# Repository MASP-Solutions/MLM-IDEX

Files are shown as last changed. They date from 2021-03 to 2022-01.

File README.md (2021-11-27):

# MLM-IDEX<br/>
MLM IDEX is a mod for Ben Levi's BLV MGN CUBE Project
<br/>
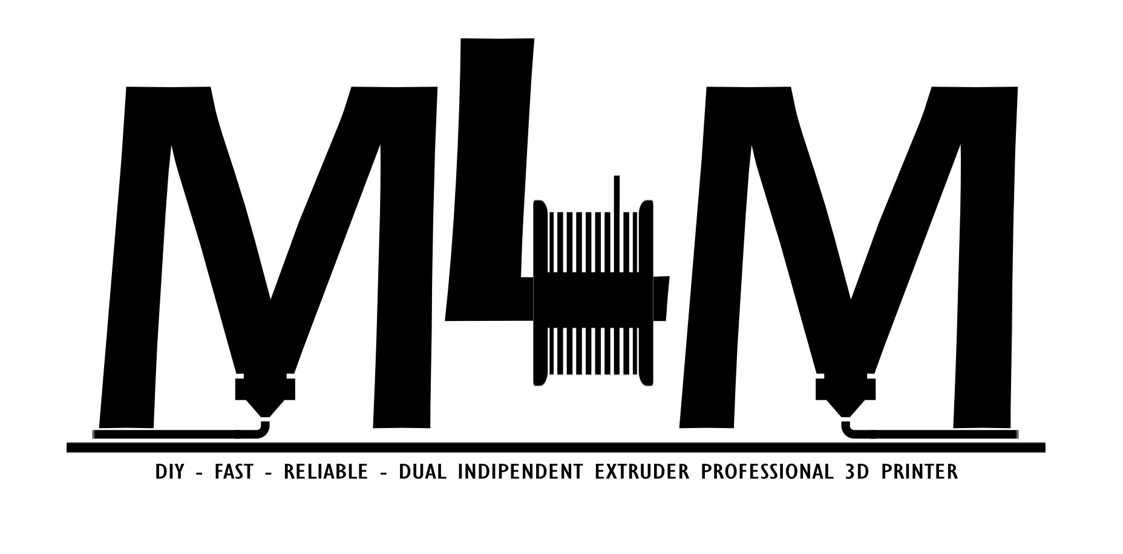
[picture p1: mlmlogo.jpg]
<br/>
<br/>
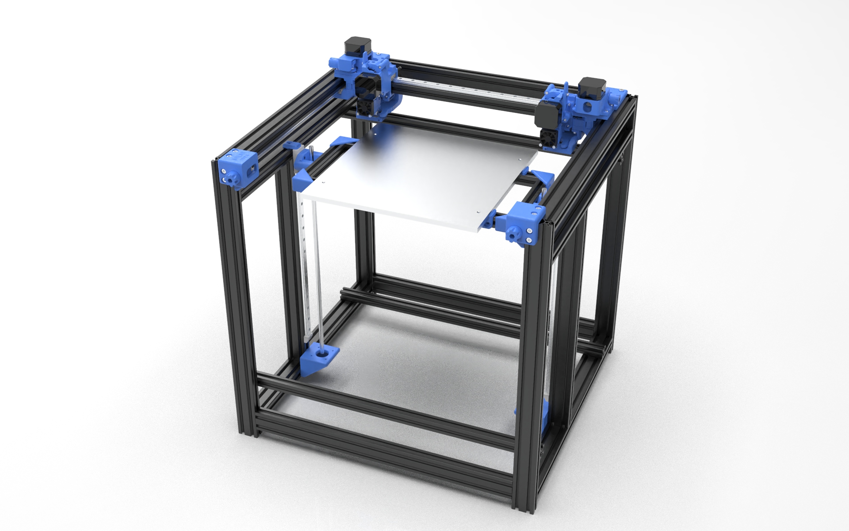
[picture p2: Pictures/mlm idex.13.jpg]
<br/>

## English<br/>
BLV MLM IDEX is a italian project started in August 2020 in collaboration with Maicol Spazzini (MASP-Solutions), Loris Granatella and Mario Salerno.<br/> 
We redesigned Ben Levi's BLV MGN Cube and created an IDEX version.<br/> 
This printer allows you to create copy, mirror and IDEX configuration prints (using two different colours or materials).<br/>
The MLM IDEX is equipped with MASP Hotend MK8-R All Metal with adjustable titanium throat, Duet 2 Wi-Fi, Duex5.<br/>
The X and U axes are driven by powerful LDO Motors 0.9° 1.4A pancakes that allow 800/step rotations.<br/>
The same ones are also used for E0 and E1, combined with a specially designed dual drive system.<br/>
The Y-axis is driven by two Wantai 0.9° 2.4A motors working in pairs: the advantage is the possibility to move the x/u bridge at high speeds and without uncertainties, also thanks to the use of a robust 9mm reinforced GT2 belt (Gates Powergrip).<br/>
Regarding the X- and U-axes, 6mm GT2 (Gates Powergrip) belts were used to reduce space requirements and to have less moving mass than the Y-axis.<br/>
A cleaning system tied to the X/U bridge ensures that the inactive tool nozzle can purge outside the plate (tool parking area) and cleans the nozzle before it enters the printing area.<br/>
The calibration of the Z offset, for "Tool 0" (i.e. X), is semi-automatic thanks to the use of a contact probe (BLTouch) and a procedure written by us ad hoc to facilitate the operation. As for the "Tool 1" (i.e. U) the calibration of the Z offset is manual, effectively facilitated by the constructive conformation of the MASP MK8-R hotend.<br/>
It is possible to choose between two or three trapezoid screws, driven by powerful Wantai 1.8° 2.5A motors.<br/>
The plate heater is a 600W - 220V "membrane" type, the top is made of 6mm aluminium.<br/>
The project is open source, all the necessary parts are freely available for purchase and printing.<br/>
The project provides all the files for the configuration that we have developed after months of testing.<br/>
## [Watch the project in 3D](https://a360.co/3cTrbso) 

## Italiano<br/>
MLM IDEX è un progetto nato ad Agosto 2020 in collaborazione con Maicol Spazzini (MASP-Solutions),  Loris Granatella e Mario Salerno, nel quale abbiamo riprogettato la BLV MGN Cube di Ben Levi creandone una versione IDEX.<br/> 
Questa stampante permette di creare stampe in copia, in mirroring e stampe in configurazione IDEX (due colori o materiali differenti).<br/>
MLM IDEX è equipaggiata con MASP Hotend MK8-R All Metal con gola in titanio regolabile, Duet 2 Wi-Fi, Duex5.<br/>
Gli assi X ed U sono azionati da potenti pancake LDO Motors 0,9° 1.4A che permettono di avere 800/step giro, gli stessi sono utilizzati anche per E0 ed E1, abbinati ad un sistema dual drive realizzato ad hoc.<br/>
L'asse Y è azionato da 2 motori Wantai 0,9° 2,4A che lavorano in coppia, a vantaggio di ciò, la possibilità di muovere il ponte X/U senza incertezze e ad alte velocità, garantito anche dall'impiego di una robusta cinghia da 9mm rinforzata di tipo GT2 (Gates Powergrip).
Per quanto concerne gli assi X ed U, sono state impiegate cinghie da 6mm di tipo GT2 (Gates Powergrip) per ridurre gli ingombri e per la minor massa in movimento rispetto all'asse Y.<br/>
Un sistema di pulizia vincolato al ponte X/U fa in modo che l'ugello del tool non attivo possa spurgare al di fuori del piatto (tool parking area) e pulisce l'ugello prima del suo ingresso nell'area di stampa.
La calibrazione dell'offset Z, per il "Tool 0" (ovvero X), è semiautomatica grazie all'impiego di una probe a contatto (BLTouch) e ad una procedura scritta da noi ad hoc per facilitare l'operazione, per quanto riguarda il "Tool 1" (ovvero U) la calibrazione dell'offset Z è manuale, agevolata efficacemente dalla conformazione costruttiva dell’hotend MASP MK8-R.<br/>
E' possibile scegliere se movimentare l'asse Z servendosi di due o tre viti trapezie, azionate da potenti Wantai 1.8° da 2.5A.<br/>
Il riscaldamento del piatto è di tipo a "membrana" da 600W - 220V, il piano in alluminio fresato da 6mm.<br/>
Il progetto è open source, tutte le parti necessarie alla realizzazione del progetto sono liberamente acquistabili e stampabili.<br/>
Il progetto mette a disposizione tutti i file per la configurazione che abbiamo messo a punto dopo mesi di collaudo.<br/>
## [Esplora il progetto in 3d](https://a360.co/3cTrbso)

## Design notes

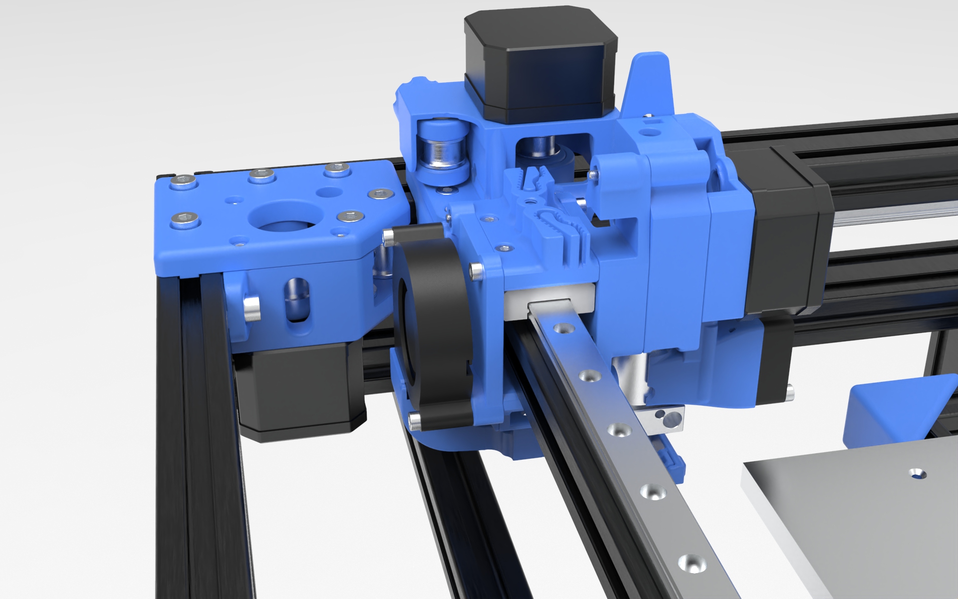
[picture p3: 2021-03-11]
Pictures/mlm idex.17.jpg

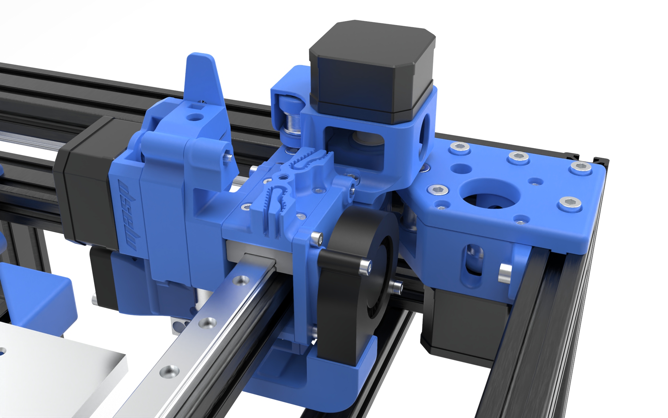
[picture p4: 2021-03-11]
Pictures/mlm idex.16.jpg

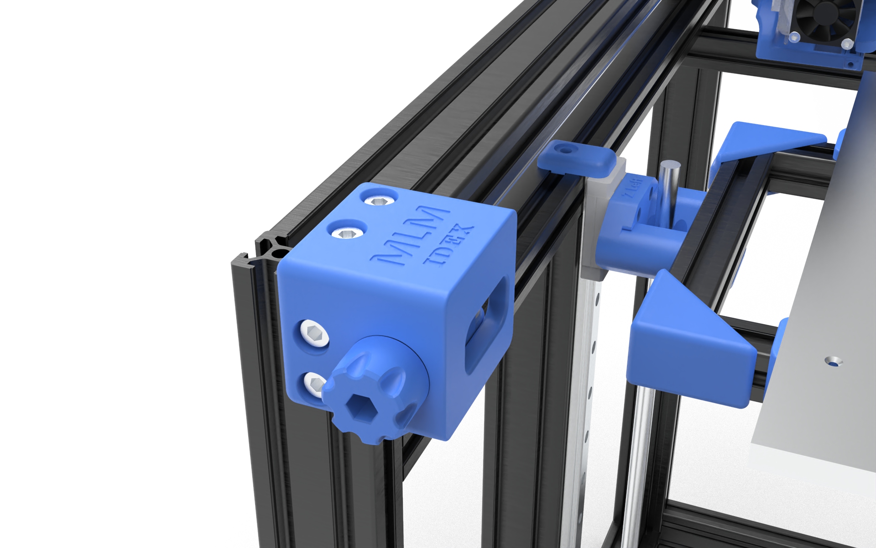
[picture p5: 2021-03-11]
Pictures/mlm idex.14.jpg

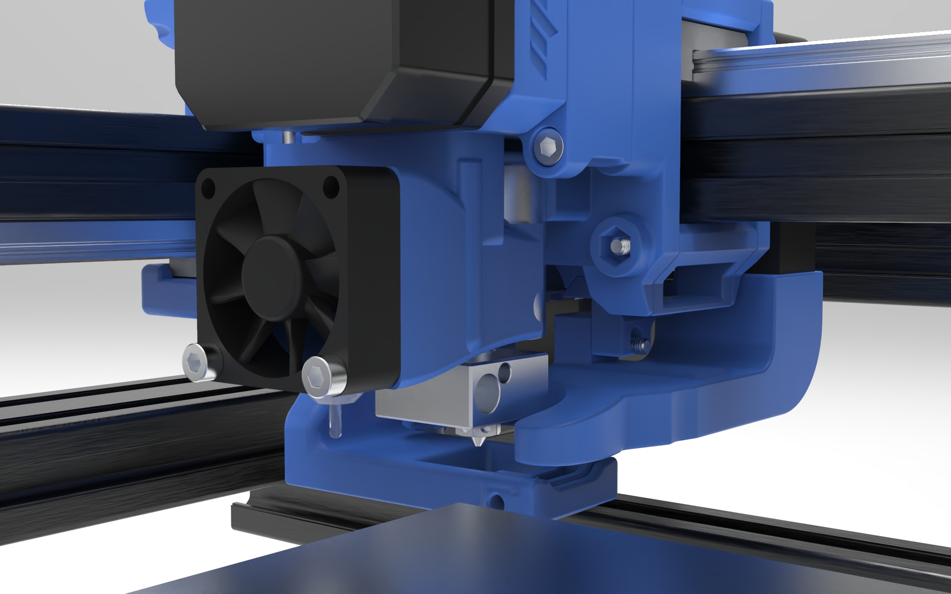
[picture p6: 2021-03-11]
Pictures/mlm idex.18.jpg

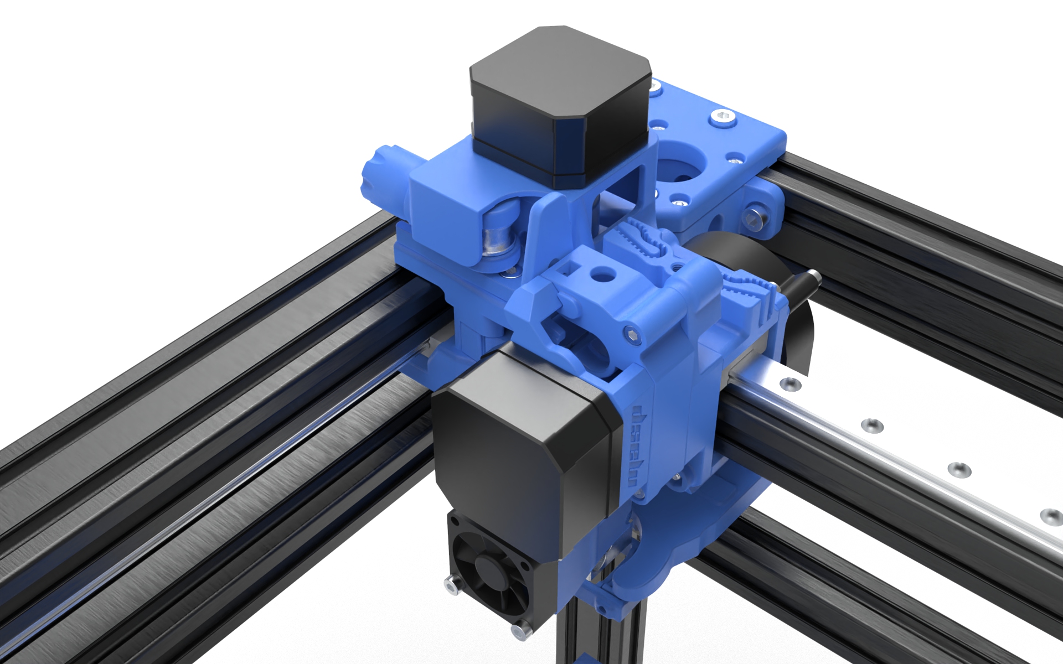
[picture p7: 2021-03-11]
Pictures/mlm idex.15.jpg

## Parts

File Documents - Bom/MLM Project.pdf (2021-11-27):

Doc. ver. 20211118

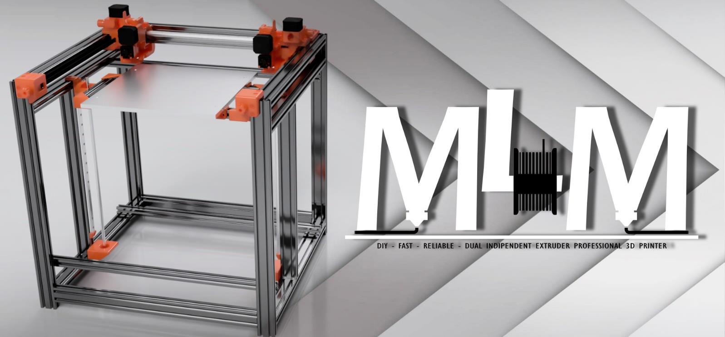
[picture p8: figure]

MLM Version 1.2

## Bill of materials and other informations

Note. This document deals with what is necessary to carry out the project as originally conceived with the standard BLV frame 310x310x365 (print area)

## Index

## Bill of materials

### Components

Quantity Product name | Type / Aliexpress choice | Link 1 Link 2
1 | BLV MGN Cube blind joint frame kit | 365 Dual Z axis | Link (https://it.aliexpress.com/item/1005001591680638.html?spm=a2g0s.9042311.0.0.4e564c4dbnLPIW)
3 | Linear rails MGN12 | 400mm - MGN12H(black) | Link (https://it.aliexpress.com/item/33043386369.html?spm=a2g0s.9042311.0.0.4e564c4dbnLPIW)
1 | Additional rail block (U Axis) | H Block Only - MGN12H(black) | Link (https://it.aliexpress.com/item/33043386369.html?spm=a2g0s.9042311.0.0.4e564c4dbnLPIW)
1 | D20 L25 Couplers 5x8x25mm | 2pcs | Link (https://it.aliexpress.com/item/32967226009.html?spm=a2g0s.9042311.0.0.4e564c4dbnLPIW)
1 | Build Plate | 300x300 - 310x310 | Link (http://lecktor.com/en/v2x-buildplate/428-203-voron-2-build-plate-300x300mm.html) | Link (https://www.landwehr3d.de/shop/heizbett/praezisionsgussplatte-gebohrt) Link (https://www.aliexpress.com/item/1005001928616831.html)
1 | Magnetic bed | 310x310 | Link (https://www.amazon.it/gp/product/B07XGKRJN5/ref=ppx_yo_dt_b_search_asin_title?ie=UTF8&psc=1) | Link (https://it.aliexpress.com/item/4000065586567.html?spm=a2g0s.9042311.0.0.27424c4dyEfevq)
2 | GT2 20T Pulley Bore 5mm | For 10mm | Link (https://it.aliexpress.com/item/33023279793.html?spm=a2g0s.9042311.0.0.3fbf4c4dOUWB1H)
2 | GT2 20T Idler Bore 5mm toohless | W 11mm without teeth | Link (https://it.aliexpress.com/item/33023133633.html?spm=a2g0s.9042311.0.0.27424c4dppqWib)
4 | GT2 20T Idler Bore 5mm with teeth | W 11mm with teeth | Link (https://it.aliexpress.com/item/33023133633.html?spm=a2g0s.9042311.0.0.27424c4dppqWib)
1 | 2PCS GT2 Pulley 16T Bore 5mm with teeth | 16 teeth | Link (https://it.aliexpress.com/item/33002989677.html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)
2 | GT2 20T Idler Bore 3mm with teeth | 20T With teeth | Link (https://it.aliexpress.com/item/4000040551804.html?scm_id=1007.13339.169870.0&scm-url=1007.13339.169870.0)
1 | Gates GT2 timing belt 9mm | 4M-9MM-2GT | Link (https://it.aliexpress.com/item/32952396111.html?spm=a2g0s.9042311.0.0.27424c4dppqWib)
1 | Gates GT2 timing belt 6mm | 4M-6MM-2GT | Link (https://it.aliexpress.com/item/32952396111.html?spm=a2g0s.9042311.0.0.27424c4dppqWib)
2 | Hotend MASP MK8-R | Link (https://www.masp-solutions.it/product-page/copia-di-masp-hotend-mk8-r)
1 | Silicon 500℃ resistant (nozzle purge system) | 150x150x3mm | Link (https://www.amazon.it/gp/product/B083195M9M/ref=ppx_yo_dt_b_asin_image_o06_s01?ie=UTF8&psc=1) | Link (https://it.aliexpress.com/item/1005001817496355.html)
1 | Build plate silicon spacers | 4pcs 16ymm – color black | Link (https://www.amazon.it/HAWKUNG-Stampante-livellamento-Silicone-Compatibili/dp/B07WG6PHQS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) | Link (https://www.aliexpress.com/item/1005001823789355.html)
1 | Thermal Insulant for Heatbed | 300x300x10MM | Link (https://www.amazon.it/gp/product/B07KSYTVHM/ref=ppx_yo_dt_b_asin_image_o07_s00?ie=UTF8&psc=1) | Link (https://www.aliexpress.com/item/33002961558.html)
2 | High quality nozzle 0.4mm E3D V6 | 0.4 | Link (https://it.aliexpress.com/item/4000254386244.html)
1 | Ball bearings | 635ZZ | Link (https://it.aliexpress.com/item/32796192081.html)

### Extruders options

Quantity Product name | Type / Aliexpress choice | Link 1 Link 2

BMG
2 | BMG Direct Drive base kit | Diy Basic Kit | Link (https://it.aliexpress.com/item/4000021186440.html?spm=a2g0o.cart.0.0.5e133c00B3i5Yx&mp=1)

Sherpa Mini
2 | Fysetc sherpa mini SLS PA12 | | Link (https://it.aliexpress.com/item/1005002305932756.html)

Orbiter 1.5
2 | Fysetc Orbiter 1.5 SLS PA12 | | Link (https://it.aliexpress.com/item/1005001798573466.html)

### Z-Probes options

Quantity Product name | Type / Aliexpress choice | Link 1 Link 2

BL-Touch
1 | Antclabs BLTouch Probe | | Link (https://www.amazon.it/Antclabs-Bltouch-livellamento-sensore-stampante/dp/B01FFV2TOS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)
1 | BLTouch SM-DU extension cable | 1.5mt | Link (https://www.3djake.it/antclabs/prolunga-bltouch-sm-du)
Inductive
1 | LJ12A3-4-Z/BX | Link (https://it.aliexpress.com/item/32987128959.html)

### Z axis options

Quantity Product name | Type / Aliexpress choice | Link 1 Link 2

### 2 screws based z axis

2 | Fysetc T8 POM leadscrew | Lead2mm 400 | Link (https://it.aliexpress.com/item/1005002055526955.html)
2 | Linear rails MGN12 | 400mm - MGN12H(black) | Link (https://it.aliexpress.com/item/33043386369.html?spm=a2g0s.9042311.0.0.4e564c4dbnLPIW)

### 3 screws based z axis

3 | Fysetc T8 POM leadscrew | Lead2mm 400 | Link (https://it.aliexpress.com/item/1005002055526955.html)
3 | GT2 Pulleys 20T + Pulley 40T Kit | Option 1: 20T(6mm)-40T(8mm) Option 2: For belt width 6mm | Link (https://it.aliexpress.com/item/4000683278512.html)
3 | GT2 Belts 200mm | Option 1: 6mm Option 2: 200-2GT-6 RF Option 3: 1 pcs | Link (https://it.aliexpress.com/item/4000397043382.html)
3 | Linear rails MGN12 | 400mm - MGN12H(black) | Link (https://it.aliexpress.com/item/33043386369.html?spm=a2g0s.9042311.0.0.4e564c4dbnLPIW)

### Main Electronics options

Quantity Product name | Type / Aliexpress choice | Link 1 Link 2

Duet 2 + Duex5
1 | Duet2 Wifi V1.04 32bit | Link (https://it.aliexpress.com/item/32879765446.html?scm_id=1007.13339.169870.0&scm-url=1007.13339.169870.0)
1 | Duex5 DueX expansion board with TMC2660 | Link (https://it.aliexpress.com/item/32888956750.html)

Duet 3 Based
1 | Duet 3 6HC + Duet 3 3HC kit | Link (https://it.aliexpress.com/item/1005001714705257.html)

Optional: Toolboard
2 | Duet Toolboard 1LC 1.0 (1.1 it’s ok as well) | Link (https://it.aliexpress.com/item/1005002458993763.html)
1 | Duet Distribution board | Link (https://it.aliexpress.com/item/1005002741266202.html)

### Electronics

Quantity Product name | Type / Aliexpress choice | Link 1 Link 2
1 | MeanWell LRS-350-24 PSU PSU 24V 350w | | Link (https://it.aliexpress.com/item/33045665308.html?spm=a2g0s.9042311.0.0.4e564c4dbnLPIW)
1 | SSR-25DA | | Link (https://it.aliexpress.com/item/32663806352.html?spm=a2g0s.9042311.0.0.4e564c4dbnLPIW)
1 | SSR-40DA | | Link (https://it.aliexpress.com/item/32663806352.html?spm=a2g0s.9042311.0.0.4e564c4dbnLPIW)
1 | Heated silicon bed 310x310 | 220v 750watt | Link (https://www.amazon.it/gp/product/B07RHGXWDZ/ref=ppx_yo_dt_b_asin_title_o00_s00?ie=UTF8&th=1) | Link (https://www.aliexpress.com/item/1005001709811375.html)
1 | Thermal fuse 10A 250V - 172 °c | 5 Pieces – 15A – 165C | Link (https://www.amazon.it/gp/product/B08HMDCR56/ref=ppx_yo_dt_b_search_asin_title?ie=UTF8&psc=1) | Link (https://www.aliexpress.com/item/32893092186.html)
1 | 2PCS Blower Gdstime 5015 50mm DC 24V | 24V Ball 5000RPM | Link (https://it.aliexpress.com/item/32841967974.html)
1 | 5PCS Fan Gdstime DC 24V 3cm 30x30x10mm | 0.06A3010B24V2P2.54 | Link (https://it.aliexpress.com/item/32814252396.html)
1 | Display PanelDue 5i / 7i | | Link (https://it.aliexpress.com/item/4000164026031.html?scm_id=1007.13339.169870.0&scm-url=1007.13339.169870.0)
1 | Wantai 3 PCS Stepper Nema17 42BYGHM810 0.9° | 3PCS-42BYGHM810 | Link (https://it.aliexpress.com/item/33057503469.html?spm=a2g0s.9042311.0.0.27424c4dppqWib)
1 | Wantai 5 PCS Stepper Nema17 42BYGHW811 1.8° | | Link (https://it.aliexpress.com/item/32664250308.html?spm=a2g0s.9042311.0.0.27424c4dppqWib)
4 | LDO Stepper Nema17 0.9 LDO-42STH25-1404MAC | | Link (https://www.jacksfilament.com/LDO-Nema-17-SLIM-POWER-09-Pancake-Motor-LDO-42STH25-1404MAC)
1 | Power button 16mm | 220V Self-reset Momentary | Link (https://it.aliexpress.com/item/32676526568.html?spm=a2g0s.9042311.0.0.27424c4ddjDWID)
2 | Ceramic Cartridge Heater | 24V 50W 2M | Link (https://it.aliexpress.com/item/32829216441.html)
2 | Termistore E3D-E-SEMITEC-50-MOLEX-INC-CABLE | | Link (https://www.3djake.it/e3d/termistore) | Link (https://www.aliexpress.com/item/32847452724.html)
1 | MicroSD Memory (for the board) | 1gb min. | Link (https://www.amazon.it/gp/product/B08BKCB4JW/ref=ppx_yo_dt_b_asin_title_o05_s00?ie=UTF8&psc=1) | Link (https://www.aliexpress.com/item/32855791603.html)
1 | AC Power switch with fuse | 1PC witch cable | Link (https://www.amazon.it/gp/product/B07RRY5MYZ/ref=ppx_yo_dt_b_asin_title_o09_s01?ie=UTF8&psc=1) | Link (https://www.aliexpress.com/item/32857063415.html)
1 | Limit Switch Roller | | Link (https://it.aliexpress.com/item/32966619156.html)

### Hardware

Quantità Nome articolo | Tipologia / Opzione Aliexpress Link 1 Link 2
100 | M3x8 | Screw
20 | M3x10 | Screw
20 | M3x12 | Screw
20 | M3x16 | Screw
20 | M3x20 | Screw
20 | M3x25 | Screw
20 | M3x30 | Screw
10 | M3x35 | Screw
12 | M3x40 | Screw
4 | M3x45 | Screw
2 | M3x50 | Screw
12 | M4x10 | Screw
6 | M4x25 | Screw
50 | M5x8 | Screw
4 | M5x20 | Screw
6 | M5x30 | Screw
6 | M5x35 | Screw
100 | M3 T-Nut | T-Nut
50 | M5 T-Nut | T-Nut
30 | M3 Nut | Nut
30 | M4 Nut | Nut
20 | M5 Nut | Nut
4 | M3x35 | Flat head screw
50 | M3 Washers | Washers
50 | M4 Washers | Washers
50 | M5 Washers | Washers

## 3D project realtime view

In order to see every single detail about this project, click here: https://a360.co/3cTrbso

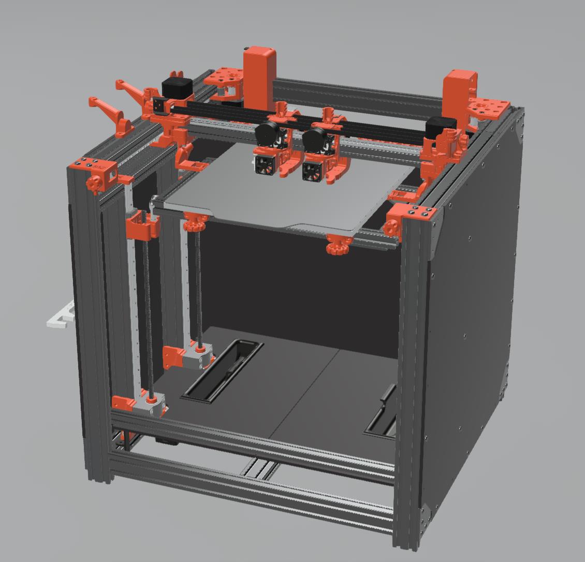
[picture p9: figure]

## Printed parts placement

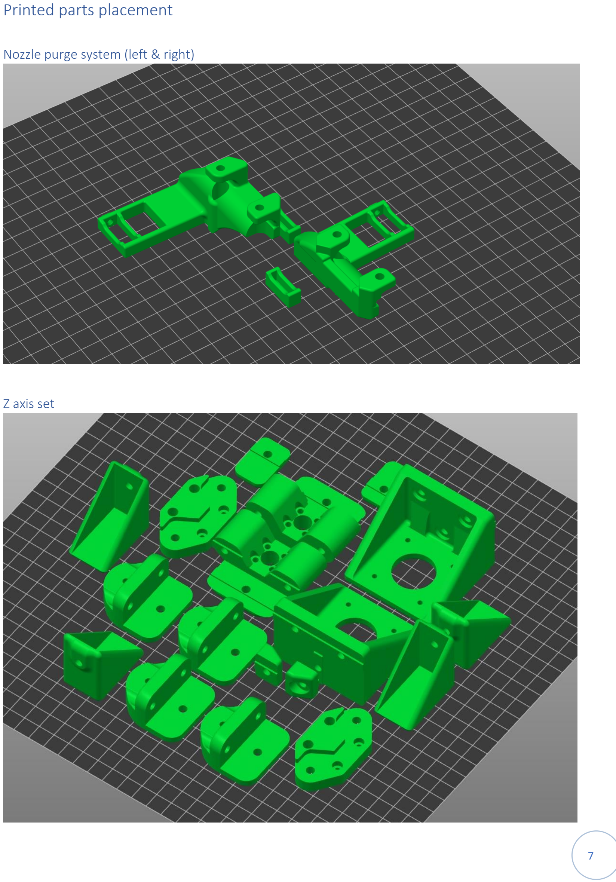
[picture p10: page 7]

### Nozzle purge system (left & right)

### Z axis set

### Right extruder set (U axis)

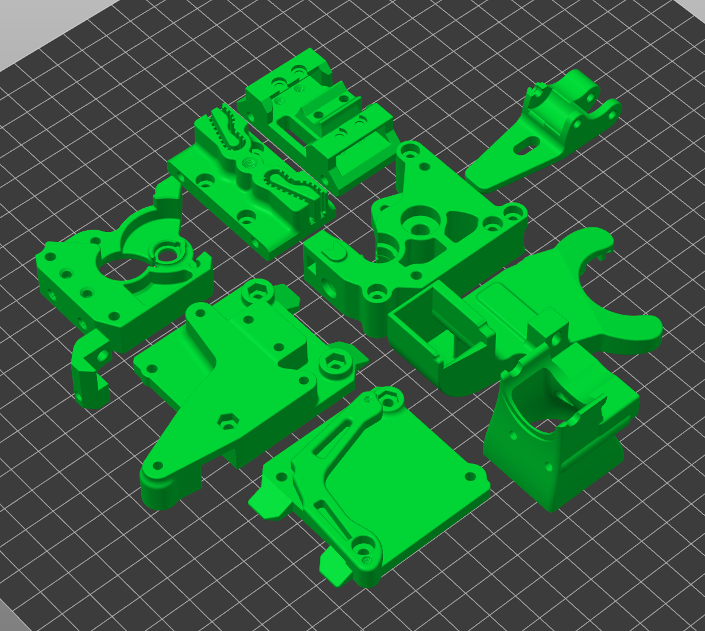
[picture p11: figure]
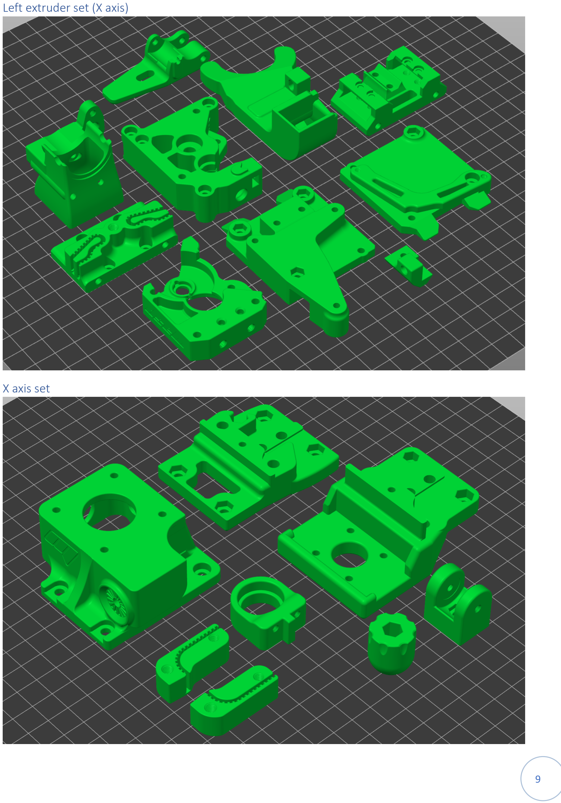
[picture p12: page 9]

### Left extruder set (X axis)

### X axis set

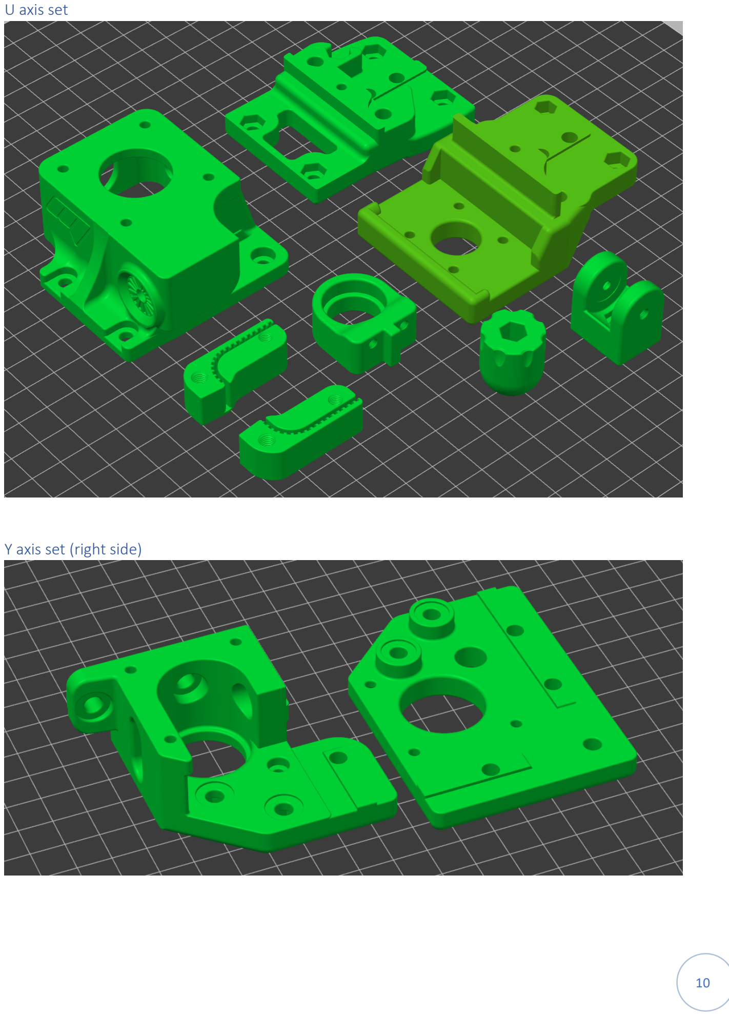
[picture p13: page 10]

### U axis set

### Y axis set (right side)

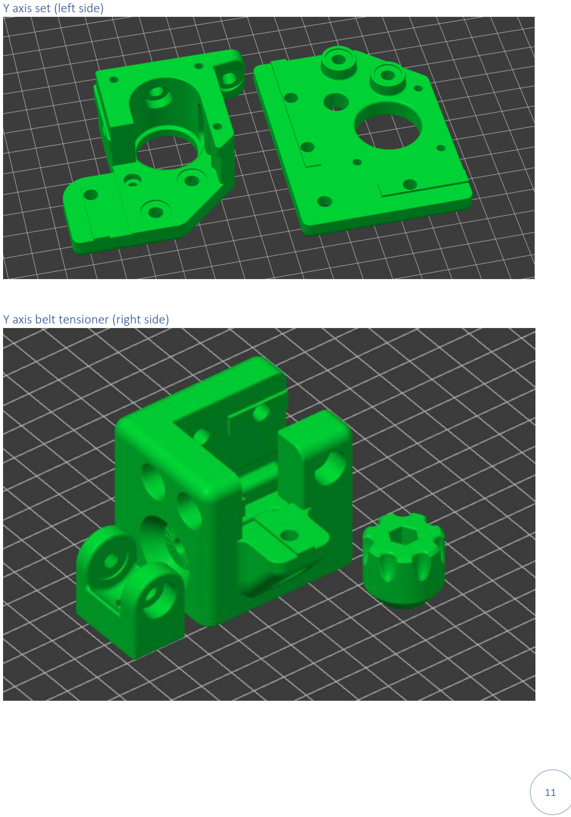
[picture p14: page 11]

### Y axis set (left side)

### Y axis belt tensioner (right side)

### Y axis belt tensioner (left side)

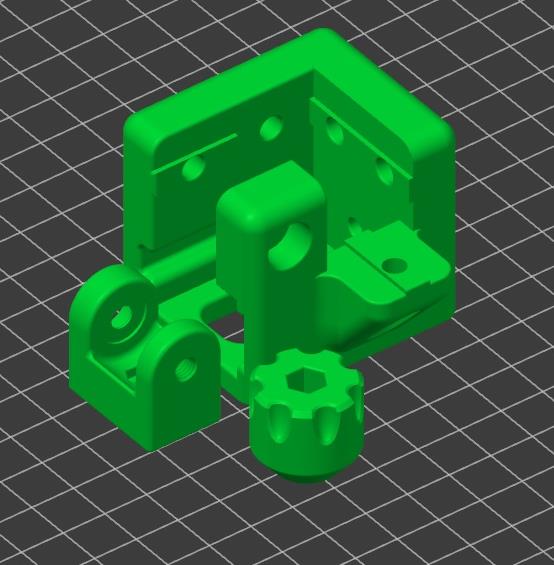
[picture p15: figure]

## Power – Wiring diagram


## Heated bed – Wiring diagram


## Duet Distribution board (optional) – Wiring diagram


## Duet Toolboard 1LC 1.0 (optional) – Wiring diagram


## Duet Toolboard 1LC 1.1 (optional) – Wiring diagram


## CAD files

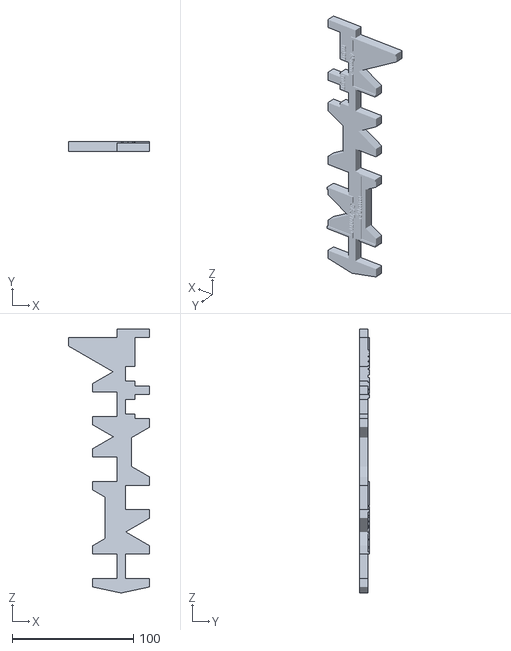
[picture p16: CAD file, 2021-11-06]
MLM Parts/STL/Other/Jigs/Jig_Main.stl
67.0 x 8.00 x 217.8

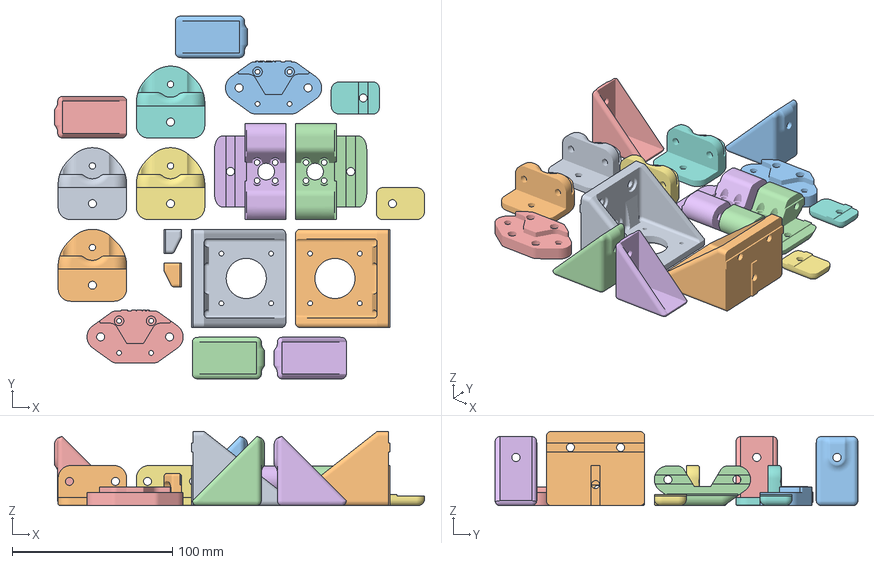
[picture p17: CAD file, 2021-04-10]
BLV IDEX PARTS/3MF/supporto piatto.3mf
230.7 x 226.3 x 46.2 mm
C:/Users/saler/AppData/Local/Temp/Neutron/d9faab0f-9fc9-49fd-b756-813e63f718b9.stl_1
C:/Users/saler/AppData/Local/Temp/Neutron/d9faab0f-9fc9-49fd-b756-813e63f718b9.stl_2
C:/Users/saler/AppData/Local/Temp/Neutron/d9faab0f-9fc9-49fd-b756-813e63f718b9.stl_3
C:/Users/saler/AppData/Local/Temp/Neutron/d9faab0f-9fc9-49fd-b756-813e63f718b9.stl_4
C:/Users/saler/AppData/Local/Temp/Neutron/d9faab0f-9fc9-49fd-b756-813e63f718b9.stl_5
C:/Users/saler/AppData/Local/Temp/Neutron/d9faab0f-9fc9-49fd-b756-813e63f718b9.stl_6
C:/Users/saler/AppData/Local/Temp/Neutron/d9faab0f-9fc9-49fd-b756-813e63f718b9.stl_7
C:/Users/saler/AppData/Local/Temp/Neutron/d9faab0f-9fc9-49fd-b756-813e63f718b9.stl_8
C:/Users/saler/AppData/Local/Temp/Neutron/d9faab0f-9fc9-49fd-b756-813e63f718b9.stl_9
C:/Users/saler/AppData/Local/Temp/Neutron/d9faab0f-9fc9-49fd-b756-813e63f718b9.stl_10
C:/Users/saler/AppData/Local/Temp/Neutron/d9faab0f-9fc9-49fd-b756-813e63f718b9.stl_11
C:/Users/saler/AppData/Local/Temp/Neutron/d9faab0f-9fc9-49fd-b756-813e63f718b9.stl_12
C:/Users/saler/AppData/Local/Temp/Neutron/d9faab0f-9fc9-49fd-b756-813e63f718b9.stl_13
C:/Users/saler/AppData/Local/Temp/Neutron/d9faab0f-9fc9-49fd-b756-813e63f718b9.stl_14
supporto piatto (2).stl

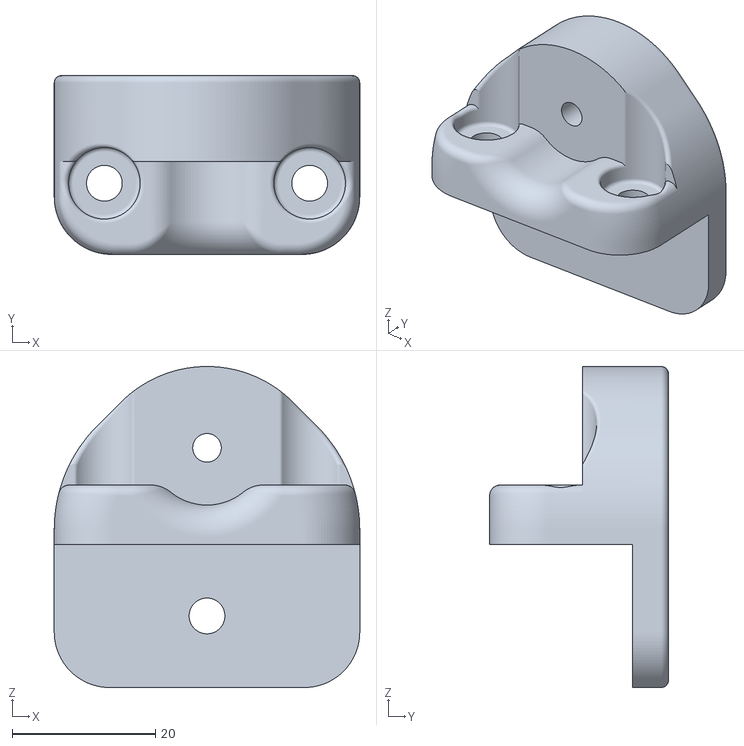
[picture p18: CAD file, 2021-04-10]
MLM Parts/STL/Bed/supporto piatto.stl
42.7 x 25.0 x 44.9

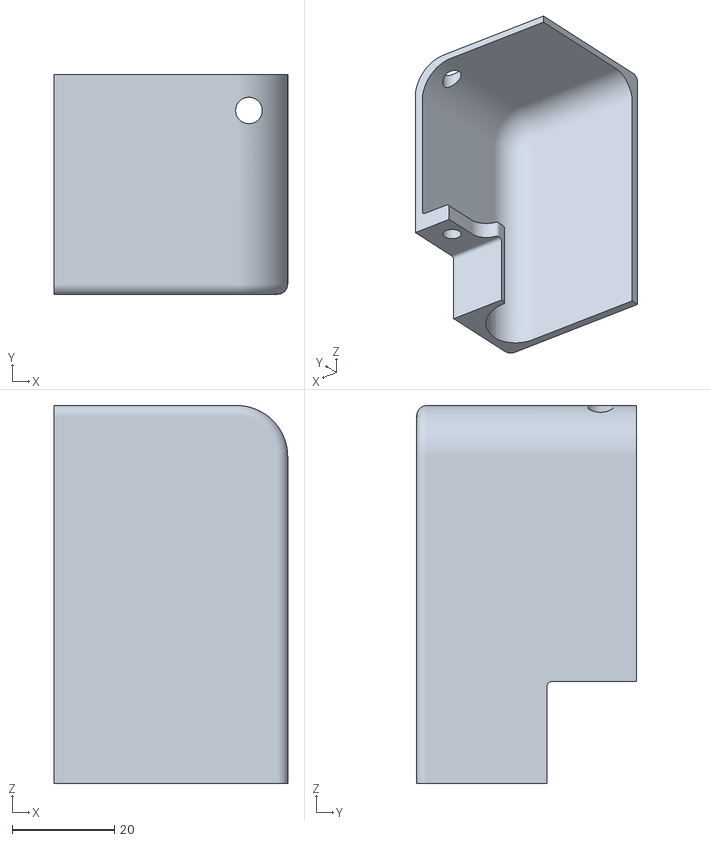
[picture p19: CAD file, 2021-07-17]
MLM Parts/STL/Cablechain stuff/Asse Y/Copertura supporto catena SX - HIGH.stl
45.7 x 43.0 x 74.0

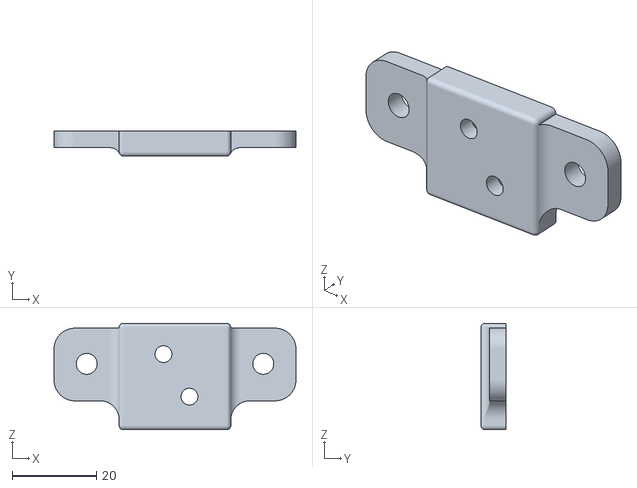
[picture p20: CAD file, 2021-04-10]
MLM Parts/STL/Cablechain stuff/Letto/Attacco catena 20x10 chiusa aliexpress - Lato Letto.stl
57.6 x 6.00 x 25.3

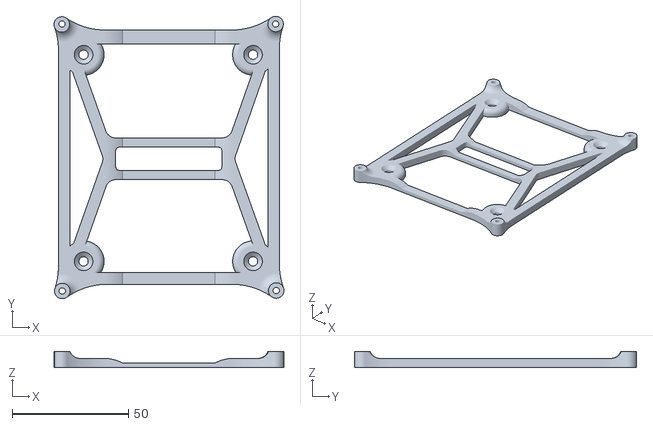
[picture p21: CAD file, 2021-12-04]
MLM Parts/STL/Electronic stuff/Supporto Duet 3 Mini.stl
99.1 x 121.7 x 7.00

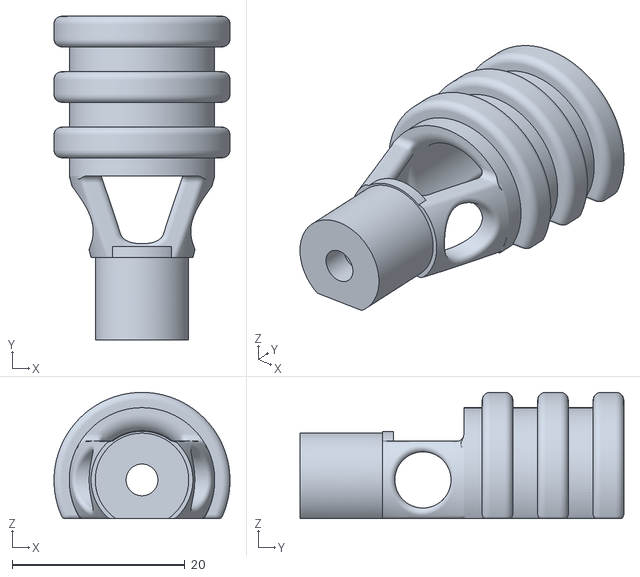
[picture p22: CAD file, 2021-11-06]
MLM Parts/STL/Extruders/Common/Supporto Fascia Cavi - Tool v2.stl
20.3 x 37.4 x 14.6

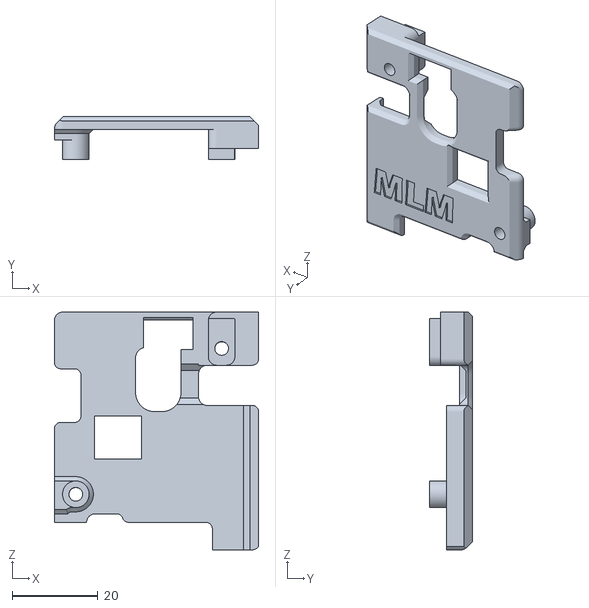
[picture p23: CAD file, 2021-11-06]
MLM Parts/STL/Extruders/Common/ToolBoard Mod/pcb_cover toolboard 1.0. High version.stl
47.6 x 10.00 x 55.5

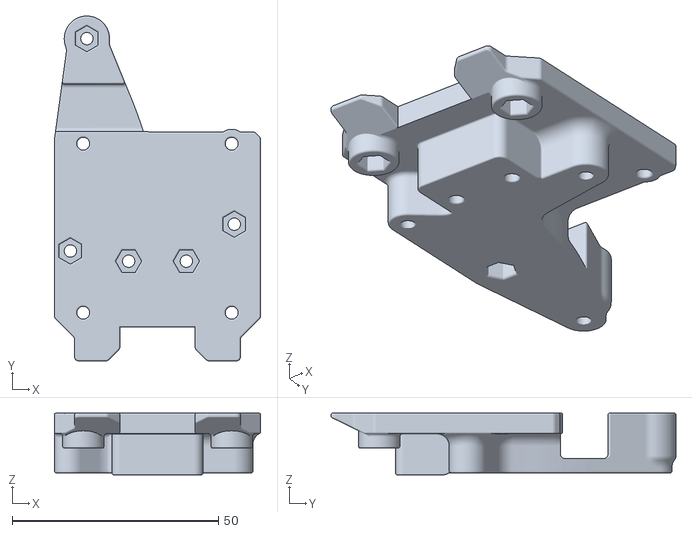
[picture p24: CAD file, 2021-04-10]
MLM Parts/STL/Extruders/Specific - BMG Based Extruder/Paratia Anteriore.stl
50.0 x 83.7 x 15.0

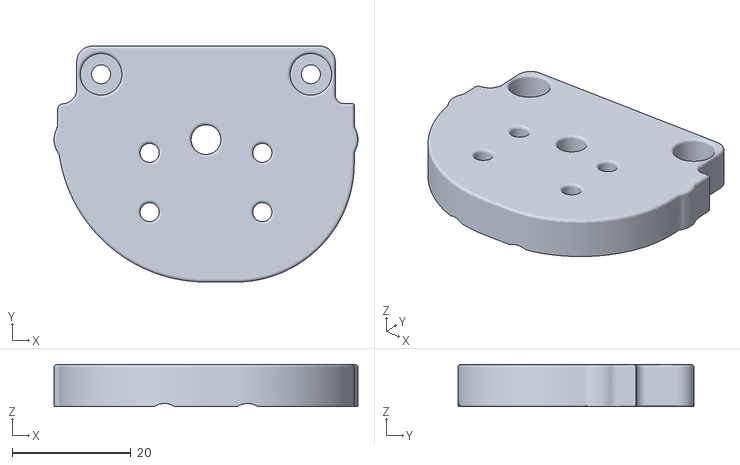
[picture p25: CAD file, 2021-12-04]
MLM Parts/STL/Extruders/Specific - Bondtech LGX Lite/LGX Lite Mount.stl
51.2 x 39.8 x 7.10

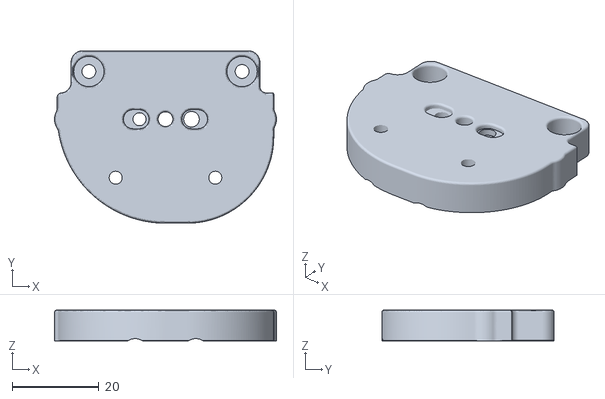
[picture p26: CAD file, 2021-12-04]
MLM Parts/STL/Extruders/Specific - Bondtech LGX/LGX Mount.stl
51.2 x 39.8 x 7.10

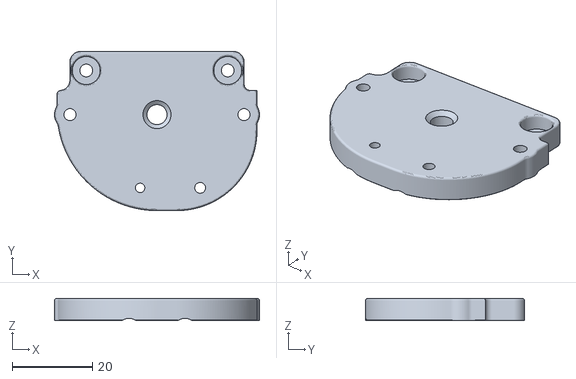
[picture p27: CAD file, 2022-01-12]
MLM Parts/STL/Extruders/Specific - Libra Mini (Mellow Sherpa)/Libra Mini Mount.stl
51.2 x 39.8 x 5.50

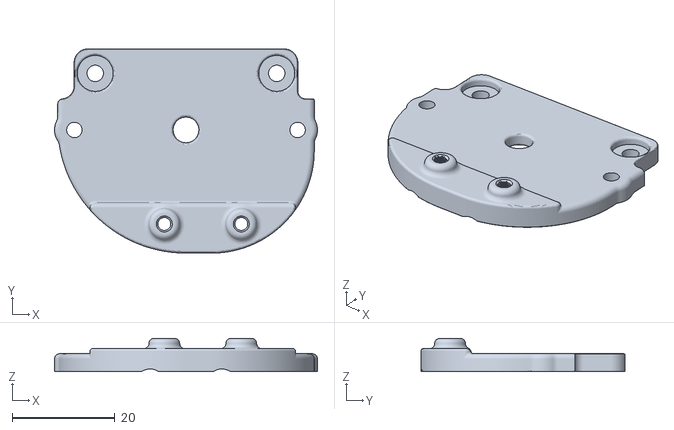
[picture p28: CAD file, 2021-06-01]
MLM Parts/STL/Extruders/Specific - Sherpa Mini/Sherpa Mount.stl
51.2 x 39.8 x 6.50

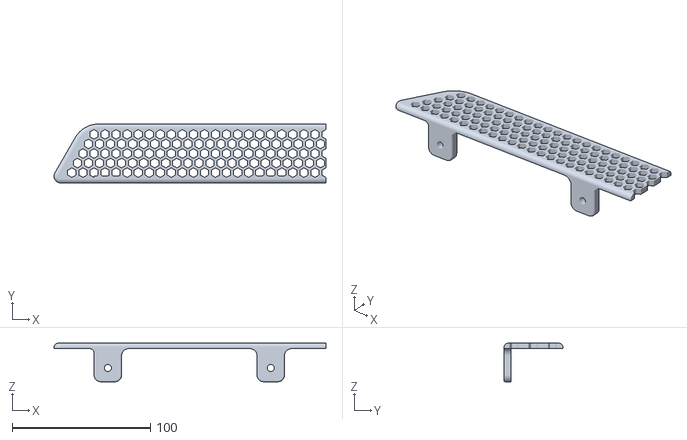
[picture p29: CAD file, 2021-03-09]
MLM Parts/STL/Front panels/Pannello Frontale Paneldue 7 + controller/Left Grid.stl
197.0 x 42.8 x 28.0

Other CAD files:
MLM Parts/STL/Extruders/Specific - Orbiter 1.5/Orbiter 1.5 LEFT Mount.stl
MLM Parts/STL/Extruders/Specific - Orbiter 2.0/Orbiter 2.0 Mount.stl
MLM Parts/STL/Front panels/Pannello Frontale Paneldue 7i/Left Panel.stl
MLM Parts/STL/Other/Alimentazione filo laterale.stl
BLV IDEX PARTS/3MF/Bracci_pulitura_nozzle.3mf
BLV IDEX PARTS/3MF/Insieme_asse_Z.3mf
BLV IDEX PARTS/3MF/Supporto_Y_DX.3mf
BLV IDEX PARTS/3MF/Supporto_Y_SX.3mf
BLV IDEX PARTS/3MF/Tensionatore_Y_DX.3mf
BLV IDEX PARTS/3MF/Tensionatore_Y_SX.3mf
MLM Parts/3MF (obsolete)/Bracci_pulitura_nozzle.3mf
MLM Parts/3MF (obsolete)/Insieme_asse_Z.3mf
MLM Parts/3MF (obsolete)/Supporto_Y_DX.3mf
MLM Parts/3MF (obsolete)/Supporto_Y_SX.3mf
MLM Parts/3MF (obsolete)/Tensionatore_Y_DX.3mf
MLM Parts/3MF (obsolete)/Tensionatore_Y_SX.3mf
MLM Parts/STL/Bed/Agolare telaio.stl
MLM Parts/STL/Cablechain stuff/Asse Y/Copertura supporto catena DX - HIGH.stl
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

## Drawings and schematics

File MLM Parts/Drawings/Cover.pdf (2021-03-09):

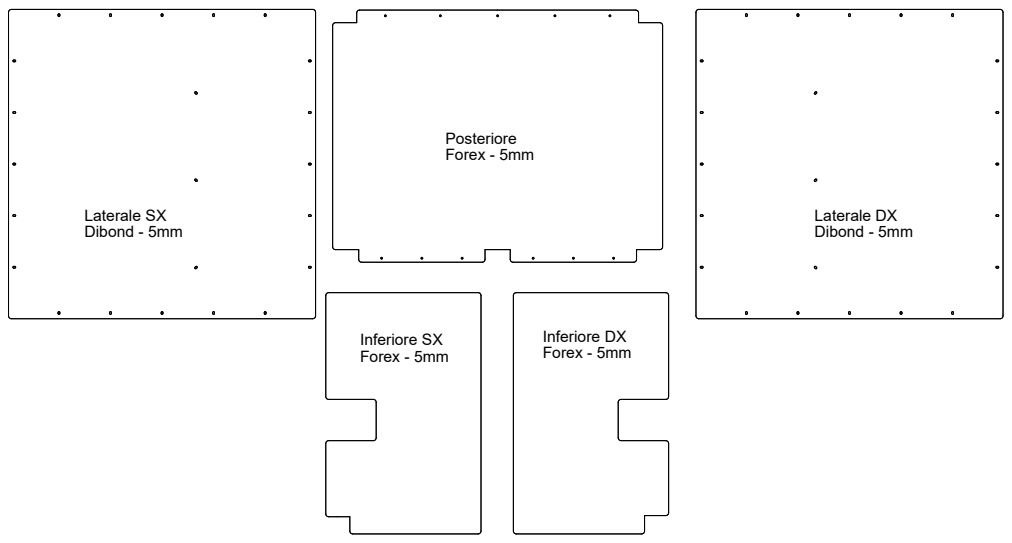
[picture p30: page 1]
Laterale SX Dibond - 5mm; Laterale DX Dibond - 5mm; Posteriore Forex - 5mm; Inferiore SX Forex - 5mm; Inferiore DX Forex - 5mm

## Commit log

2021-03-09 Release 1
    [Alimentazione filo laterale.stl, Bracci_pulitura_nozzle.3mf, Center Panel.stl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]
2021-04-10 stl aggiunti
    [Agolare telaio.stl, Alimentazione filo laterale.stl, Ancoraggio Cinghia Y frontale - SX.stl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]
2021-04-10 catene passacavo
    [Attacco catena 20x10 chiusa Amazon.stl, Attacco catena 20x10 chiusa aliexpress - Lato Letto.stl, Attacco catena 20x10 chiusa aliexpress - Lato Telaio.stl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]
2021-04-11 braccio pulizia dx ok
    [Braccio pulizia DX.stl, Braccio pulizia DX_fixed.stl]
2021-04-13 Aggiornati supporti ventole e bom
2021-04-14 Aggiunto supporto duet 2 wifi
    [Supporto Duet 2 Wifi.stl]
2021-04-14 Create Supporto Duex5.stl
    [Supporto Duex5.stl]
2021-04-21 Inseriti scassi T-Nut negli inviti dei profilati
    [Angolare Inferiore DX.stl, Angolare Inferiore SX.stl, Angolare superiore DX.stl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]
2021-04-24 Aggiunto ancoraggio CableChain
    [Ancoraggio Cinghia Y frontale - SX.stl, Ancoraggio Cinghia Y frontale.stl, Ancoraggio Cinghia Y frontale_fixed.stl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]
2021-04-24 Castelletto motore DX sistemato
2021-04-25 Supporto sx cablechain y
    [Supporto Catena 20x10 Telaio SX.stl]
2021-04-29 Added missing stl
    [Agolare telaio.stl, Alimentazione filo laterale.stl, Ancoraggio Cinghia Y frontale - SX.stl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]
2021-05-09 cablechain system updated
    [Copertura supporto catena DX.stl, Copertura supporto catena SX.stl, Supporto svolgimento catena + Alimentazione filo.stl]
2021-05-09 add m6 filament tube holder
    [Supporto svolgimento catena + Alimentazione filo M10.stl, Supporto svolgimento catena + Alimentazione filo M6.stl]
2021-05-14 New stuff
    [884.03.2.07 - Duct 5015.stl, 884.03.2.09 - Supporto Duct v2.stl, Griglia Posteriore Superiore - Destra.stl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]
2021-05-16 Y Endstop
    [EndStop Y.stl, Supporto Fascio Cavi DX.stl, Supporto Fascio Cavi SX.stl]
2021-05-26 New Y Belt Tensioner
    [Corpo Tendicinghia frontale DX - Slim.stl, Corpo Tendicinghia frontale SX - Slim.stl, Slitta Tendicinghia frontale - Slim.stl]
2021-06-01 1.2 RC1
    [884.03.2.07 - Duct 5015.stl, 884.03.2.09 - Supporto Duct v2.stl, Coperchio Estrusore.stl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]
2021-06-02 update 1.2 RC2
    [Braccio pulizia DX.stl, Supporto Duct v2.stl]
2021-06-13 Create Reggicuscinetto Angolare Y.stl
    [Reggicuscinetto Angolare Y.stl]
2021-06-13 rename folder
    [Corpo Tendicinghia frontale DX - Slim.stl, Corpo Tendicinghia frontale DX.stl, Corpo Tendicinghia frontale SX - Slim.stl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]
2021-11-06 3 axis belt Z and Toolboard mounts
    [4010 - FanDuct - U Axis.stl, 4010 - FanDuct - X Axis.stl, BK10 - 8mm.stl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]
2021-11-06 Jigs updated
    [2020_Jig.stl, 2040_Jig.stl, Jig - Z - Back Left.stl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]
2021-11-06 Updated extruders
    [Carriage - High Connection.stl, Carriage - Low Connection.stl, Duct 5015.stl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]
2021-11-11 Update Orbiter Mount.stl
    [Orbiter Mount.stl]
2021-12-04 LGX Lite support
    [LGX Lite Mount.stl, Orbiter Mount.stl, Sherpa Mount.stl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]
2021-12-04 Duet 3 Mini Mount added
    [Supporto Duet 3 Mini.stl]
2021-12-04 Create LGX Mount.stl
    [LGX Mount.stl]
2021-12-08 Updated Y belt tensioners, introduced pin mod for pulleys
    [Corpo Tendicinghia frontale DX - Slim.stl, Corpo Tendicinghia frontale SX - Slim.stl, Pomello tensionatore x2.stl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]
2021-12-11 updated y tensioners
    [Corpo Tendicinghia frontale DX - Slim.stl, Corpo Tendicinghia frontale SX - Slim.stl, Slitta Tendicinghia frontale Y - Slim - (Pin 5x20) x2.stl]
2021-12-31 Orbiter 2.0 Mount
    [Orbiter 2.0 Mount.stl]
2022-01-12 adde right orbiter 1.5 mount
    [Libra Mini Mount.stl, Orbiter 1.5 LEFT Mount.stl, Orbiter 1.5 RIGHT Mount.stl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]
